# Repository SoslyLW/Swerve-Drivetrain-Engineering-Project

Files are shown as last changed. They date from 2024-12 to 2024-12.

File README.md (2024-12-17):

# Swerve Drivetrain Engineering Project
This repo contains the SOLIDWORKS model and reports for a swerve drivetrain developed for the Queen's University VEX Robotics Team, QVEX.

## Important Files
- The complete assembly of the drivetrain can be found at [`Solidworks Files > Drivetrain > Model.SLDASM`](https://github.com/SoslyLW/Swerve-Drivetrain-Engineering-Project/blob/main/Solidworks%20Files/Drivetrain/Model.SLDASM) 
- To see motion simulations of the wheel and gears in motion, see the file [`Solidworks Files > Motion Study > Motion With Materials.SLDASM`](https://github.com/SoslyLW/Swerve-Drivetrain-Engineering-Project/blob/main/Solidworks%20Files/Motion%20Study/Motion%20With%20Materials.SLDASM)
- The final project report can be see at [`Reports > SwerveDrivetrainFinalReport.pdf`](https://github.com/SoslyLW/Swerve-Drivetrain-Engineering-Project/blob/main/Reports/SwerveDrivetrainFinalReport.pdf)  (warning, it's 37 pages...)

## Explanation of a "Swerve Drivetrain"
**What is it?**

A swerve drivetrain is a type of drivetrain that can rotate it's wheels in any direction to allow complete freedom of motion.

**What types are there?**

There are 3 basic types of swerve drivetrains: direct drive, transmission, and differential. This design is a differential swerve drive.

**How does it work?**

In a differential swerve drive, each wheel is driven by 2 motors connected to 2 main gears (top and bottom) gear which are connected to 2 pinion gears which connects to the axle. When the 2 main gears rotate in the same direction, the wheel will turn in that direction. When the 2 main gears rotate in opposite directions, the wheel will spin according to the gear speed difference. By combining how you power the main gears you can make the wheel drive and turn in any direction.

See these examples below:

**Driving**

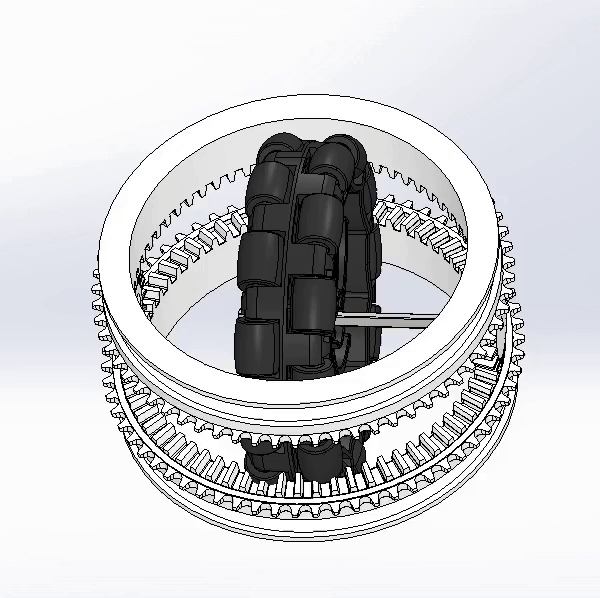
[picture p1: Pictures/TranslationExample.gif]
Wheel moving forward


**Turning**

Wheel turning

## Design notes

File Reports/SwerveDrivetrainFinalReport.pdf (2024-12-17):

# Swerve Drivetrain

# QVEX

# Group 737 Team A

## Arandjel Dimitrijevic

## Joellie Duffy

## Megan Marshall

## Avery McFadden

## Logan White

## Evelyn Morin

## Zach Elman

# April 4, 2022

### “We do hereby verify that this written report is our own individual work and contains our own original ideas, concepts, and designs. No portion of this report has been copied in whole or in part from another source, with the possible exception of properly referenced material”

i

## Executive Summary

When competing in VEX robotics, an effective and efficient drivetrain design is crucial to a team’s success. The QVEX team is interested in the use of a swerve drivetrain as this design produces a higher torque resulting in better competition results as opposed to other drives. A swerve drivetrain allows each wheel to have free rotation while being able to move forward. There are many configurations of the swerve drivetrain such as the direct, transmission, and differential drives. Through a decision matrix, the differential design was chosen over the direct and transmission due to their wiring and spacing challenges. Although this design is complex, its low profile and cost will give the QVEX team an advantage.

The differential drive has many 3D printed parts and can be easily implemented with the existing robot. The design features two aluminum mounting plates that encased the motors, wheels, and function as the mounting points to the chassis. There are also two gears (upper and lower) powered by a pinion gear attached to the motor shaft that provided torque through rotation and turned the robot by rotating at different speeds.

Custom base gears were designed to cater to the four-inch omni-directional wheel and the VEX generic chain and sprocket kit. The specific relations and measurements of these gears were calculated using research about VEX parts as well as bevel gears. The motor mounts and plates were also custom designed to account for specific height requirements, hole placement, and compatibility with the gear system.

The construction of the physical prototype was completed with some alterations due to unforeseen compatibility issues. The QVEX team was consulted to supply certain VEX parts, but the omni-directional wheels had rollers that exceeded four inches in diameter, and they were only able to supply high-strength chains. As a result, the design was altered to use a gear in the place of chains and a standard 4” wheel instead of an omni-directional one. The mounting plate and virtual model were updated to agree with the new design.

Testing was completed on the virtual model through various Solid works simulation software that analyzed the model’s motion, static capability, and sustainability. These sections and the financial analysis were all tested and scored appropriately based on quantifiable specifications that the group set earlier. All sections were scored from one to five, with a score given by how well the model performed in each of these sections. As a result, a scaled equation was used to combine the four sections into one number that determined whether the model was a successful swerve drivetrain. The model received a cumulative score of 3.4, meaning that client expectations were met and, in some cases, exceeded. For further implementation, it is recommended that the gear system is scaled for the omni-directional wheel and all metal parts are welded during construction.

ii

## Table of Contents

iii

iv

## List of Tables

Table 1: Table of stakeholders and their influence towards the project | 2
Table 2: Bill of materials for a quarter section of the swerve drivetrain | 5
Table 3: Decision matrix used to evaluate different swerve drivetrain configurations | 9
Table 4: List of purchased items and their costs | 14
Table 5: Work breakdown structure | 22
Table 6: Evaluation Rubric for the Testing Phase for the Model | 30

## List of Figures

Figure 1: Quarter section side view of the final differential swerve design | 4
Figure 2: Top view of a quarter section of the differential drive train | 4
Figure 3: CAD model of the final swerve drivetrain assembly, to be used in virtual testing | 5
Figure 4: Preliminary sketch of the direct drive | 6
Figure 5: Preliminary sketch of the transmission drive | 7
Figure 6: Original concept design for the differential swerve drive | 8
Figure 7: Physical prototype of the teams swerve drivetrain | 11
Figure 8: Static analysis of the bottom base gear | 15
Figure 9: Static analysis of the top the base gear | 15
Figure 10: Static analysis of the pinion gear | 16
Figure 11: Sustainability of the model using Japan as the region of exported materials | 17
Figure 12: Individual Contributions to the Phase 4 Report | 19
Figure 13: Timeline for the Client Presentation and Phase Three Completion | 23
Figure 14: Completion of the Status Reports and the start of Phase Four | 23
Figure 15: Timeline of the completion of Phase Four Part Two and the Design of the Drive | 24
Figure 16: Timeline for the completion of Phase Four and the design | 25
Figure 17: Timeline of the submission of Phase Four | 26
Figure 18: Original project timeline for the second half of the semester | 26
Figure 19: Timeline for the testing phase of the design | 27
Figure 20: Timeline for the testing phase of the virtual CAD and the build of the physical prototype......27
Figure 21: Reference diagram for gear calculations | 28
Figure 22: Measurements for hole placements on the motor mount and mounting plate. All
measurements in millimeters | 29

## Part 1: Key Information for Clients

## 1.1 Problem Statement and Scope Definition

### Problem Definition

VEX Robotics is a competition in which two teams of robots will attempt to score as many points as possible during the match to beat the opposing robots. During the latest competition, VEX points can be scored by placing rings on towers and moving the towers to a team's respective base. For many years VEX competitors have had two main drive trains, the tank drive and X drive configuration. The tank drive has more pushing power by keeping the wheels parallel to the direction of movement, whereas the X drive has less torque, but it can move and strafe in any direction. Alternately, the swerve drivetrain design can move in any direction with the wheels parallel to the movement allowing it to maximize the pushing force of the robot. The QVEX team is requesting a swerve drivetrain design as it will elevate their performance in competition in multiple ways.

### Problem Scope

With the given time and expectations from both the client and project manager, the group completed a CAD model of the swerve drivetrain that was tested through various simulations. The team physically constructed a quarter of the model to ensure that the physical prototype results resembled the ones obtained from the virtual testing simulation.

Client’s Needs
The client requested a swerve drivetrain, 18” x 18” in size, as noted in the VEX robotics competition guidelines. QVEX also requested that the drivetrain could maintain constant orientation while having complete operation mobility at no loss of speed or power. Since space was limited, the model required optimization in size, limiting moving parts and sturdiness. The client also suggested looking into gear ratios and power transfer methods to succeed in designing a successful drivetrain. As a final deliverable, a CAD (Computer-Aided Design) model of a single section of the drive was created and evaluated. Upon completion of the CAD model, a real version of the swerve was created. The model had to be tested as well, either using MATLAB or by physically building the model and completing testing in person. The swerve drivetrain was specifically chosen to maximize power and mobility, resulting in a more agile and competitive robot.

Constraints
- The drivetrain must be able to be built for under $100 and as light as possible (mostly 3D printed parts except for chassis and shafts)
- The drivetrain must be able to produce enough power to compete against other robots.
- All parts must be able to attach to the chassis without interfering with existing components
- The chassis cannot exceed 24” x 24”
- No more than 12 motors can be used while eight is the recommended amount

Functional Requirements
- Be able to switch between modes/directions of movement quickly and efficiently.
- Be able to have the wheels parallel to the direction of travel to maximize power like a Tank drive
- Be able to strafe and move in any direction like an X drive
- Be legal in competition
- The prototype is of at least one section of the drive
- Minimum 4 motors, maximum 12 (ideally 8)
- Build is recommended under 18” x 18”

Relevant Stakeholders
Table 1: Table of stakeholders and their influence towards the project
Stakeholder | Influence on the design process
QVEX | The team will use the design in competition, and it can improve their gameplay. Success in the competition will encourage more students to join the club and will increase funding from the university. The team has set out design requirements for elements they are looking to include such as wheels that are able to rotate independently and the robot is able to move in diagonal lines. The requirements laid out will ensure the drivetrain is compatible with the rest of their design.
VEX Robotics | The rules set out by the VEX robotics competition will constrain the design in terms of chassis/drivetrain size and available components.
Opponents | The opponents are looking to defeat the QVEX team by designing a robot with more torque, higher speeds, and greater ease of maneuverability. The clients' design must be stronger than the opponents in all aspects to defeat them. Since some opponents are expected to use tank-style drivetrains with more torque, this design must be optimized to have the ability to deliver as much torque as possible to maintain proper positioning while the opponent is attacking. The stake of the opponents overlaps with the stake that the Faculty of Engineering and Applied science holds. For the design to be superior to all opponents, it may become very costly and require materials the university isn’t providing.
Queen’s University Faculty of Engineering and Applied Science | The faculty will be investing in the QVEX design and gameplay. The design will need to be within the designated budget set out by the University. If the team is successful in their quest to build a robot containing a swerve drivetrain, it will provide the university with publicity, and presents the potential for the school to draw in more students eager to work and compete with QVEX. The stake of the faculty will overturn the stake of the opponents, without the funding provided by the university, the QVEX team would not be able to develop the design and compete.

## 1.2 Background Information

### Drivetrains

Designing any type of drive train poses the challenge of getting the power from the motor to the wheel. One way of transferring this power is using an indirect transmission system by attaching a belt to the shaft of the DC motor, then attaching that belt to the shaft of a caster. This can also be achieved using bevel gears which results in the motor undergoing far less stress [1]. In the chosen design, it means that the belt can be attached to the motor and then connected to the large driving gears that will be surrounding the wheels. While modifying the gears, the goal of having the swerve drivetrain with all four wheels turning, steering, and driven independently is still the number one priority. This allows the robot to move in any direction with its full pushing force, as the wheels can be parallel to the direction of movement. For a traditional swerve drivetrain to operate, there needs to be one motor to spin the wheel forward and one to pivot the wheel and change direction [2].

### Swerve Drivetrain

An issue commonly associated with swerve drivetrains is the lack of power output when the robot is turning [3]. This disadvantage can be minimized with the use of a differential swerve drive configuration. A differential swerve drivetrain has many advantages, such as it can use both gears to drive, which will allow the robot to have more power. This design takes advantage of the power output of the differential systems which will allow the team to spin the top gear and bottom gear at different speeds, effectively turning and powering the robot simultaneously. Another advantage of this design and using 3D printing is that it allows the drivetrain to be very compact as the larger gears can be placed very close together [4]. One drawback of the swerve drivetrain is that the mass is significantly higher than other drivetrain configurations [5]. The weight can be minimized by 3D printing as many parts as possible.

### Modeling

For modeling, the program SolidWorks is the most accessible and simple platform to use. The generic VEX parts (gears, belts, motors) can be downloaded and imported from any VEX CAD library which reduces design time since these parts can be complicated [6]. To simplify the online model creation, SolidWorks offers its own robotics section within the software that allows for simple and effective VEX construction [7]. SolidWorks also offers e-drawings that can be used to clearly show the client how the design operates from multiple angles, and if a physical prototype is not able to be constructed, these drawings can be used for the QVEX team to easily build it themselves.

## 1.3 Design Solution

The chosen design was the differential swerve drive. This was chosen based on criteria identified in the decision matrix, as seen in Table 3. More specifically, after many conceptual iterations, the team settled on the design see in Figure 1 and Figure 2.

In this design, the drivetrain is supported vertically using ball bearings placed on axles. Custom horizontal gears were designed with a groove on the outside for the bearings sit in to allow free, mostly frictionless movement. The two base gears are powered by motors that are mounted to the top mounting plate using custom motor mounts. The motors turn chains that interlock with teeth on the outside of the base gears.

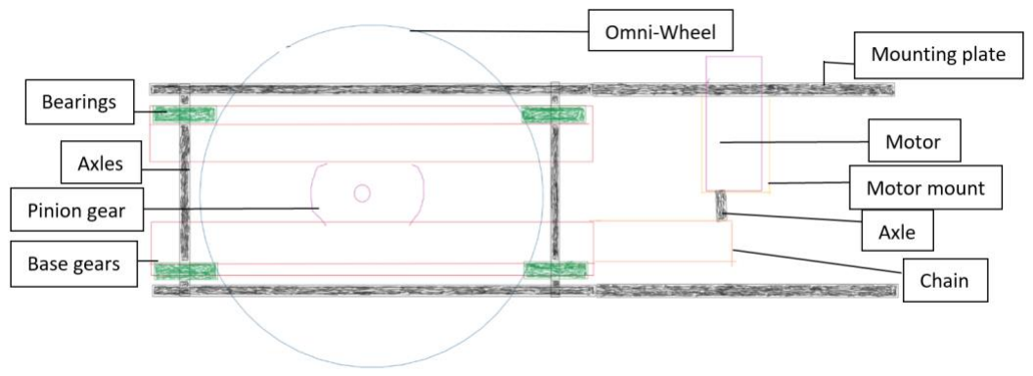
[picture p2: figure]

Figure 1: Quarter section side view of the final differential swerve design.

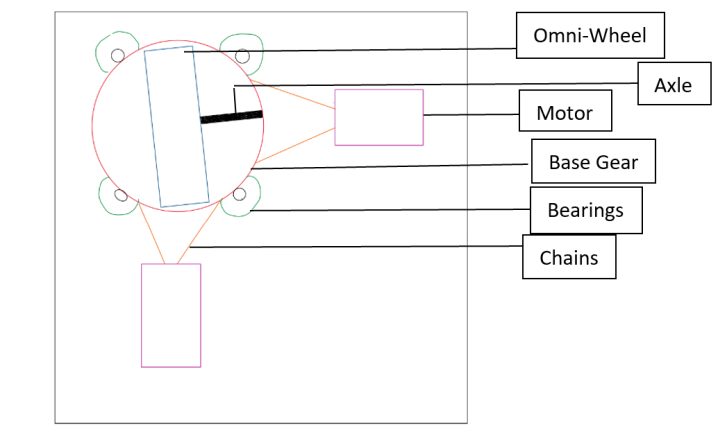
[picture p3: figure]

Figure 2: Top view of a quarter section of the differential drive train.

A CAD model was also constructed, which can be seen in Figure 3. The model was used in virtual testing to determine wheel speeds and the drivetrain’s ability to resist and support loads. The client will receive a copy of the CAD model, as well as a physical prototype. The physical prototype will display the ease of manufacturing, compactness, and whether the conceptual design will be successful once implemented. The CAD model will be used to demonstrate the drivetrains speed and turning capabilities.

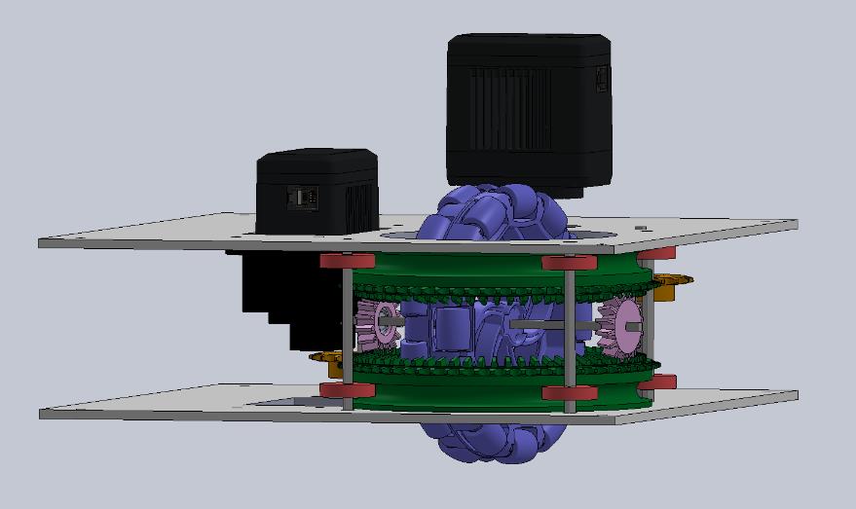
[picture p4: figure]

Figure 3: CAD model of the final swerve drivetrain assembly, to be used in virtual testing.

To implement the solution, the client would need to construct three more quarter sections, as well as mounting plates that cover the 18” x 18” base of the robot, instead of 9” x 9” sheets. Table 2 shows the bill of materials that was required to build a quarter section of the drivetrain. A written code would be required to control the speed of the individual motors, as well as the ability to reverse the direction of the motors to turn the wheels in both directions. To build the other sections, it would cost the QVEX team four times the costs outlined in Table 4, approximately $422, assuming they have access to VEX parts such as chains, motors, and wheels.

Table 2: Bill of materials for a quarter section of the swerve drivetrain.

Materials | Quantity
9” x 9” Aluminum Sheet | 2
22mm Round Radial Bearing | 8
4” Omni-directional Wheel | 1
3D Printed Custom Gears | 2
Bevel Gear | 1
Wheel Axle | 1
Bearing Axle | 4
VEX Motor | 2
VEX Chain | 2

## 1.4 Conclusions

The swerve drivetrain has intricate functions that can be executed with numerous different designs. Three main designs were considered in this project: the direct swerve drive, the transmission drive, and the differential drive. The final design was chosen based on important criteria such as cost, size, weight, and difficulty. Using a weighted decision matrix, the differential swerve drive design was found to be the best design for this project. A differential swerve drive is beneficial due to its low height and low cost. The final design is characterized by two outer gears that encircle the wheel with one upright gear between them that is attached to the axle and powers the wheel. These gears are custom designs that were 3D printed along with the motor mounts. Gears are used to power the upper and lower gears to turn and provide torque to the wheel. The wheel system is mounted to an aluminum sheet which can then be easily mounted to the chassis of the robot. Due to errors, the team went slightly over budget, spending $105.73.

The final model differed from the original design with a standard VEX wheel in place of the omnidirectional one as well as the chains being replaced with gears. These alterations were made due to incompatibility with available parts. To continue this design, it is recommended that the gear system is scaled to fit with the four-inch omnidirectional wheel. The bearings and shafts in the physical model interfere with the chain sprockets so it is recommended that thinner shafts are used with appropriate bearings of smaller inner diameter. The teeth on the upper and lower gears can be updated to be compatible with the high strength VEX chain to fulfill the original design if desired. Finally, it is recommended that the metal connections on the mounting plate are welded to ensure the longevity of the drivetrain.

## Part 2: Technical Information

## 2.1 Conceptual Design Solutions

### Design 1: The Direct Drive

This first drivetrain considered by the team was the direct drive swerve drivetrain. This design is characterized by a swivelling wheel where one motor is placed in line with the driving axle, attached to the swivel, and one motor is mounted directly to the chassis, as shown in Figure 4. The strength of this design is its simplicity. By mounting the driving motor in line with the wheel, there is no need for a transmission, drastically reducing the number of moving parts and thus the complexity. The design does have its drawbacks; one is that the wires connecting the driving motor to the chassis and VEX brain controller are unable to spin freely without tangling. To counteract this, the team went through an idea generating process and determined that a central hole through the swivelling axis would be necessary. Other design weaknesses include imbalanced loads on the axle and increased load on the turning motor.

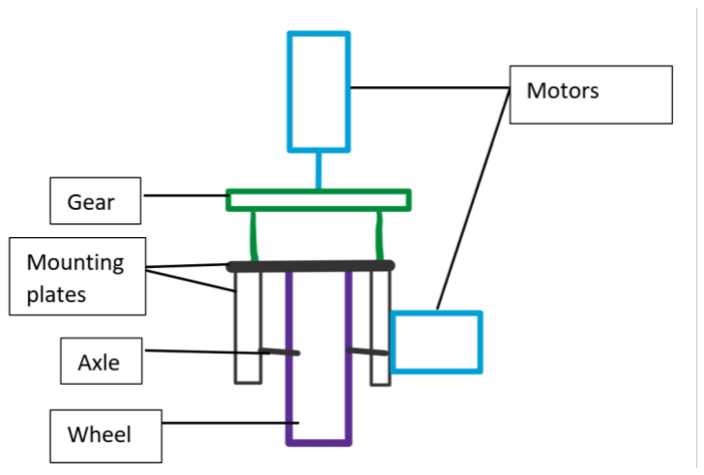
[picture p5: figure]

Figure 4: Preliminary sketch of the direct drive.

### Design 2: The Transmission Drive

The second drivetrain design conceived by the team is a type of transmission swerve drivetrain. This is another swivel-based design but features both the driving and turning motors mounted to the chassis as seen in Figure 5. Consequently, a gear-based transmission must be used to transfer the power of the driving motor to the appropriate axis. This aspect is one of the weaknesses of this design as it involves many moving parts with a need for high precision at every step. Having a transmission within a swivelling structure would also make the design much harder to repair should the transmission break. The advantage of this design is that it solves most of the issues associated with the direct drive design. This includes the issue of tangling wires, loads on the axle, and a decreased load on the turning motor.

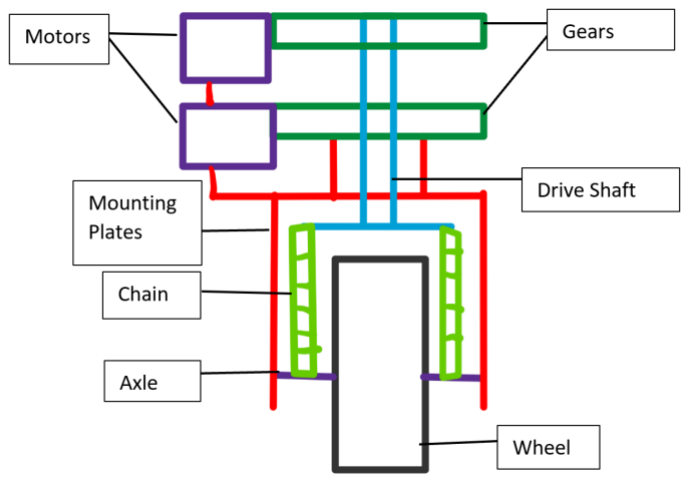
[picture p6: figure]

Figure 5: Preliminary sketch of the transmission drive.

It should also be noted that the first two design options require a large amount of vertical space. The client was consulted about this property of the designs and the team was informed that both designs are viable if properly implemented. However, if possible, the drivetrain should take up more horizontal space than vertical as to not interfere with components mounted to the chassis of the robot. This advice was considered in further idea generation and in the design evaluation matrix in Table 3.

### Design 3: The Differential Swerve

The third design option that was considered is the differential swerve drivetrain. This is a more complicated design that uses two larger horizontal gears placed around the wheel with a vertical bevel pinion gear attached to the wheel axle, in between the two horizontal gears. Each larger gear is driven independently with its own motor, allowing for differing velocities among the large gears. If the gears are moving at the same speed and in the same direction, the wheel will rotate. If the larger gears have differently velocities, the wheel will spin according to the relative difference in speed. A diagram is shown below in Figure 6. The advantages of this design are that the gears can be placed overlapping the wheel and that the motors can be placed alongside the wheel with relative ease, drastically reducing the vertical footprint of the design. Additionally, by not allocating one motor for turning and one for driving, the max turning and driving speed is increased. The drawbacks of the design are its need for custom designed gears to integrate with the rest of the robot, a time-expensive process, and the lack of space to mount and install all the components without sacrificing the benefits of the design’s compactness.

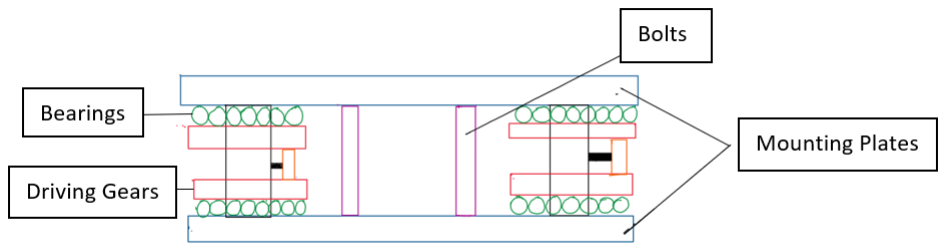
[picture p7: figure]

Figure 6: Original concept design for the differential swerve drive.

## 2.2 Decision Making

A decision matrix, as seen in Table 3, was used to compare the three design options. Each design was analyzed based on the cost, weight, complexity, and compactness. Every aspect was rated on a scale of 1-4, with the highest overall score being 16. Through this process, the team chose the differential swerve as the design proposed to be implemented due to its low weight, minimal vertical height, and low cost.

Table 3: Decision matrix used to evaluate different swerve drivetrain configurations

| Differential Swerve | Direct Drive Swerve | Transmission Swerve
Weight Optimal weight of 10lbs, maximum weight of 30 lbs [12]. | Weighs approximately 12 pounds for four-wheel design [13]. 3 | Weighs approximately 20 pounds for four-wheel design [14]. 2 | Weighs approximately 21 pounds for four-wheel design [15]. 2
Compactness Design occupies the least amount of vertical and horizontal space. | All parts will be within the height of the 4” wheels. Will be approximately 5” long by 5” wide. 4 | Design is approximately 5.5” wide, and 9.5” tall with the motors included [16]. 3 | Approximately 10” tall by 5” wide, as they allow space for the wheels, motor, and gears in the vertical direction. 2
Ease of manufacturing/ Implementation Minimize number of custom parts required, and ease of drivetrain assembly | Will be made of mostly custom 3D printed parts; however, it only consists of about 15 pieces per wheel and will be simple to assemble. 3 | Majority of parts will be made of existing metal to ensure structural integrity, can be quite complex to assemble and once assembled still has issues such as loose/excess wires. 2 | Requires many custom metal parts. The complex design will also make it very challenging to assemble. 2
Cost to Manufacture Maximum budget of $100. | Cost of 3D printed parts will be $30, and the additional metal pieces will be around $30 [8] [9], with an overall cost of $60. 4 | Majority of metal pieces need to be purchased, resulting in costs up to $120 [10]. 1 | The custom fabrication of many metal parts will exceed $180 [11]. This will exceed the set-out budget. 1
Final Weighting | 14 | 8 | 7

The low weight, minimal vertical height, and low cost make the differential swerve drivetrain the optimal solution. The differential is the design capable of producing the highest speeds and outputting the most torque, while also being relatively simple to manufacture and assemble. Due to its compactness, it is the ideal solution for QVEX which will allow them the most freedom when constructing the other components of their robot. There are also many varying components of the differential drivetrain that can be customized to fit to the exact specifications the team may be looking for. Within the differential, the team had to conclude which mounting and power transmission options would be implemented. These options have been weighed below.

### Mounting Options

Within the differential design, the team investigated different mounting options for attaching the drivetrain to the frame and the rest of the chassis. The first option investigated by the team was to use ball bearings to vertically support the gears. This would see each gear sitting on top of a mounting plate with channels in both the gear and mounting plate for the ball bearings. Unfortunately, the team could not find any VEX-approved ball bearings, so this solution was deemed inviable. The second and chosen option was to support the gears by using shafts fitted with horizontal bearings. These bearings fit into a channel in the side of the gears, allowing them to spin while being supported vertically. Since VEX does sell their own style of radial bearings, this design would both meet the team’s need and be legal as per the project constraints.

### Power Transmission Options

There were several different methods of power transmission considered for transferring the motor power to the gears. The first option was to use a gear coming directly from the motor and attach to teeth on the side of the large gears. While this option is straightforward, it lacks flexibility presented by the other options. It would necessitate a definitive placement of the motors and the gear ratio between the motor gear and the swerve drive gear would need to be fixed. The second option considered was to use a belt system attached to the motor, and around the large gears. This was eliminated due to the fear of the belt slipping and that it would also necessitate definitive motor place. The third and final power transmission method examined was a chain-based method. This was decided to be the best as it performs very similar to a belt drive with a few key advantages. Chain drives do not struggle with the same slippage as belt drives, can be shortened or lengthened to support different motor placements in the case of unexpected problems, and can be altered for behavioral adjustments.

## 2.3 Implementation

### Preliminary design

The work done after Phase 3 followed the original timeline other than the changes stated in the Contingency Plan. Due to the delay of obtaining the required physical parts, the group had to alter aspects of the design to meet the project deadline. The main dependency of this design is the custom bevel gears; hence, these were designed first. The custom gears were carefully designed with the help of supporting research that ensured the bevel-style gears would interlock properly. These calculations can be found in Appendix IV: Calculations with the corresponding diagram indicating the locations of measurements. To confirm the gears fit together, a preliminary model was constructed of the gear subsystem in SolidWorks. The system had few errors when assembled originally with only the teeth needing to be edited to account for rotational interference.

Following the design of the gears, the motor mounts and mounting plates were created, as the gears defined the specifications of these parts, such as heights and hole placements. Preliminary
measurements for the mounting plates that corresponded with the use of chains are shown in Figure 22, found in Appendix IV: Calculations. An assembly was made that included all parts of the system with imported files from the VEX website for the motor, shafts, and wheel.

### Considerations

When planning the building process for the physical model, the environmental impact of the design was taken into consideration. Since the project is a one-time-use model, it was important that many of the parts were recycled or could be used again in the future. The standard VEX parts were re-used from previous robots and other parts, such as the bearings, were minimally altered to allow for re-use in future projects. The design and testing process were created to be sufficiently thorough so that the QVEX team could implement a swerve drive into their future robots. With the ability to create a swerve drivetrain, the team could have a higher level of achievement in competition and in turn receive more funding from the university as well as inspire new team members to join. During the building process, safety precautions were taken to ensure all members were protected from harm. Safety glasses were always worn within the workshop, earplugs were worn while drilling and cutting the metal sheets, and nonworking members stayed a safe distance away from working members.

### Construction and Alterations

Since some parts of the system were unable to be printed or manufactured, the QVEX team was consulted to supply these parts. Due to 3D printing deadlines, this unfortunately happened after the custom parts were created. As a result, there were issues with the custom gears being compatible with supplied parts. When designing the base gears, a four-inch standard VEX wheel was used, however, the QVEX team was only able to supply a four-inch omni directional wheel. This wheel was incompatible with the design as the rollers on the wheel cause the diameter to be larger than four inches. For the physical model, a four-inch gear was used to simulate the function of the correct wheel so testing could proceed. The custom gears were also designed to be compatible with the basic VEX chain, however, the QVEX team could only provide the High-Strength chain, which was incompatible with the teeth created. To solve this issue, the design was altered to use gears instead of chains. These gears were 3D printed for efficiency and to ensure compatibility. The CAD assembly was altered as well by adding the correct gears and updating the mounting plate holes to account for this change. The overall model, which can be seen in Figure 7, was constructed with the implementation of these changes and was successfully completed.

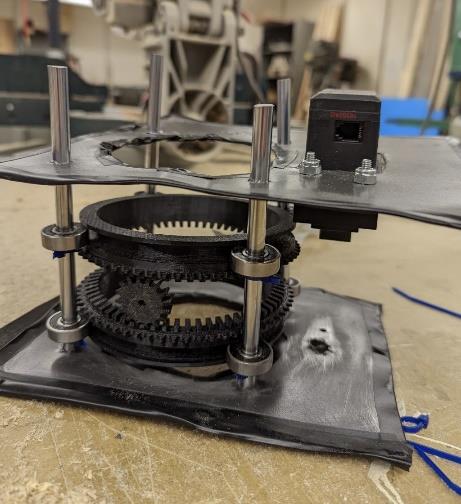
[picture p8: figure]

Figure 7: Physical prototype of the teams swerve drivetrain.

### Testing Process

After the construction of both the physical prototype and the virtual model, only the virtual model was tested to ensure the functionality of the design. The overall testing was separated into four sections for increased efficiency and organization. The first section was the motion study, which tested that the gear and wheel speeds matched the calculated predictions. The second section was the static simulation, which tested that the design could sustain the load of the robot and any unexpected exterior forces. The third section was about the sustainability and materials used, ensuring that the drive was not harmful to the environment during disposal and that the swerve could be easily reconstructed from anywhere in the world. The quantification of each section is shown in

Appendix V: Evaluation Rubric. The specific quantification of certain criteria was judged based on relative statistics given by a swerve drive with a design like the proposed model [1]. Due to unforeseen errors such as bending as a result of fabrication of the metal sheets, the physical model was unable to be tested. To provide a thorough analysis, the virtual model was more rigorously tested than originally planned with the alteration that resulting values were unable to be compared to the real system.

The virtual modelling was run on the same software that the CAD was designed in. The SolidWorks Dassault System simulation software offers a VEX tutorial course that was used by the team to efficiently test the swerve drive up to VEX standards [7]. The testing of this design focused on the functionality of the gear system, evaluating whether it can effectively spin and rotate the wheel. This specification allowed for the external parts of the system like the mounting plates, bearings, and their respective mounting shafts to be omitted. Since a simulation was used, the motor parts were replaced with simulated motion that is equivalent to what is produced from the VEX motors. After, each section (motion study, static analysis, sustainability, and financial requirements) was calculated using a weighted average using (1):

Final Score = AVGMS ∗ (0.5) + AVGSA ∗ (0.4) + AVGSUS ∗ (0.05) + AVGFR ∗ (0.05) | (1)

AVG means the average score of the motion study (MS), static analysis (SA), sustainability (SUS), and financial requirements (FR) respectively. The weightings are due to the client’s needs and that they are looking more for a functioning swerve drive that can sustain the load of their robot rather than a swerve that is very good for the environment. A final score of 1 will determine that the group has been unable to meet any needs given by the client. A score of 2 reveals that the group has made a valiant attempt but is still not quite at the level that the client requested. A score of 3 determines that the group has met all the client’s needs. A score of 4 determines that the group has exceeded the client’s expectations in most categories and that the client will be very satisfied and a score of 5 determines that the client would want to implement this design on the QVEX robot immediately. A final score of at least 3 will determine that the group has succeeded in meeting the client’s requirements and thus, has succeeded in the design.

## 2.4 Project Plan

### Work Breakdown Structure

Throughout the duration of this term, there were some events that occurred that caused a delay in project progression. This includes things like a delay arrival for the 3D printed parts, booking and software issues and many more uncontrollable variables. The team did mitigate these events at the start of the term and fell back on the second plan provided in

## Appendix III: Updated Gantt Chart and planned an updated work breakdown structure provided in

Appendix II: Project Plan.

### Risk Mitigation

After assessing the risks associated with the project completion, there were some that the group was able to mitigate. Unfortunately, due to uncontrollable errors and obstacles, there were some events that caused the group to halt or even reverse the project progression. One of these obstacles was the overall process of obtaining the physical parts to build the swerve. Due to unforeseen delays in delivering the high-strength chain, the group was forced to change the design late into the project as it was more important to have a working prototype rather than relying the entire design on one part being delivered late. As a result, the group was forced to re-iterate a design that did not implement the high-strength chain. Some risks that were mitigated with caution by the team on a consistent basis was the work done on the virtual CAD. SolidWorks is a computationally intensive program that often causes a lot of crashes at random times. The group made a valiant effort to save every file and send copies to one another so that if there was a surprise crash on the program, there would not be major setbacks in progression and backups would be available.

### Contingency Plan

The original contingency plan was that there would be two rounds of testing done on the virtual model if a physical prototype was not completed by the given deadline. Although there was an obstacle in the progression of the construction of the physical model, the group still proceeded with its construction and ran the virtual tests simultaneously to complete both by the given deadline. This was done so that the client can still have a physical prototype along with the virtual CAD model.

### Potential Changes

If this project was to be done again with the knowledge the group has now as well as assuming that the first two thirds of the project timeline was spent in person rather than online, there would be significant changes made to the design. Online communication was the root of most of the team’s obstacles since there was no simple way of getting ideas and designs across through a screen. Having team meetings take place in person from the beginning would have helped the team tremendously in having accurate specifications to the design and assuring that every group member understood what was expected of them. Although the team was content with the number of meetings that were held during the week, a change that would be made is having more meetings being centered around the production of the swerve rather than report writing. With that point being stated, having the meetings held online made it difficult to make major strides in the project completion when it is impossible to have any sort of design and implementations being made to the design when every group member is working remotely.

## 2.5 Financial Analysis

Many of the parts used in the build were recycled and therefore came at a discounted cost. The omnidirectional wheel, VEX chains, and axles were recycled from a previous robot. The VEX motors were acquired from the QVEX team with no cost. Unfortunately, due to a printing error, the original bearings and shafts purchased were incompatible, thus bearings and shafts of the correct size were purchased. This error accounts for the higher cost than previously expected. To save cost, the aluminum sheets were fashioned out of baking trays. All members of the team acquired safety trained in the shop to cut and drill the aluminum sheets at no cost.

Table 4: List of purchased items and their costs

Item | Price
Bearings | $24.27
Shafts | $29.48
Printing | $30.00
Baking trays | $21.98
| Total
| $105.73

Due to most of the project being recycled parts from previous robots, the build has a low cost in comparison to other solutions. When implementing this design, it will cost the client approximately four times what was outlined in Table 4, coming to a total of $422.92. The client may be able to save money when implementing this design if they have access to similar materials and resources, but at a discounted price.

## 2.6 Evaluation

Evaluation was done through SolidWorks simulation software. In terms of the motion study, using the gear ratio of 18:64 and a 4-inch omni-directional wheel, the model achieved a constant a velocity of 3.59m
s

. This performance scores a 3 when referring to the

Appendix V: Evaluation Rubric and meets client expectations. This result implies that the QVEX team can rely on the swerve drive’s ability to move and rotate effectively in competition at a pace that is up to their expectations.

In terms of the static analysis section, when applying a force of 270N (about 27.55kg) which is the average weight of a robot, the Solid Works static analysis simulation software produced the following stress diagrams, seen in Figure 8, Figure 9, and Figure 10. The base gears follow the teams’ expectations as the bottom gear should have most of the load placed where the pinion gear attaches, as depicted in Figure 8. The rest of the structure has an even distribution for load capabilities which concludes that the bottom gear will not undergo failure when the rest of the robot is built.

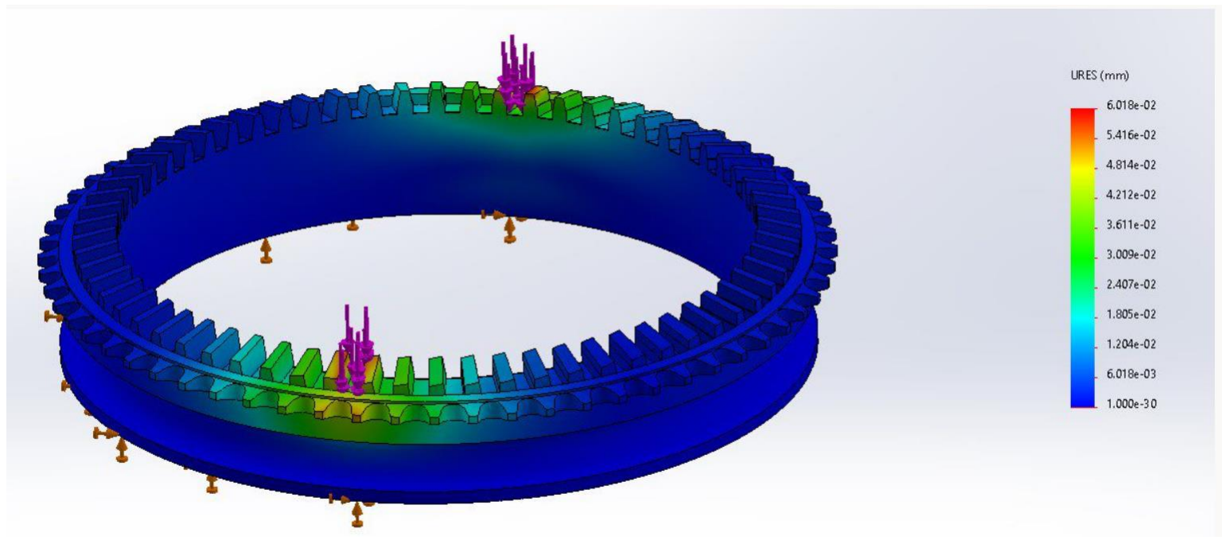
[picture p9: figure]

Figure 8: Static analysis of the bottom base gear.

The top base gear will experience a symmetrical load downwards from the weight of the attached QVEX robot and chassis. The SolidWorks analysis shows that the deflections cause by this load will be minimal using the properties of the material. The higher amount of deflection in parts of the gear are cause by the nature of how the gear is supported. Where the displacement in Figure 9 is lowest corresponds to where the two pinion gears attach to the top gear.

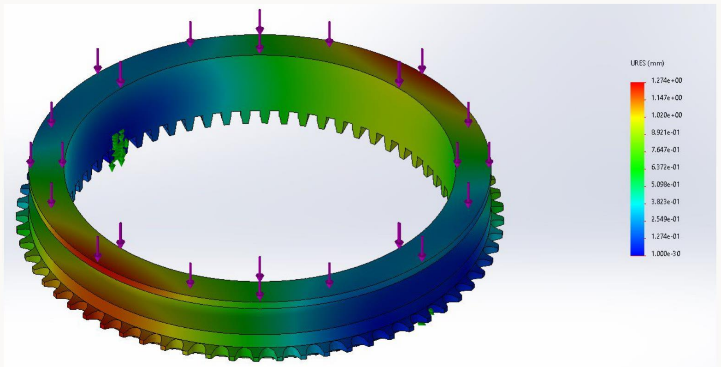
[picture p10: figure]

Figure 9: Static analysis of the top the base gear.

As for the pinion gear, for the applied load to the top gear, the pinion gear will experience a portion of the force where the pinion gear contacts the larger gear. Since there are two pinion gears in the design, the overall load is halved. Also of note, since the system is in equilibrium, the pinion gear will experience an equivalent 135 N force from the bottom gear, resisting the force that the pinion gear applies to it. The result of these forces can be seen in Figure 10. Having this symmetrical load distribution and having the pinion gear be centrally fixed through the shaft means that the pinion gear will also not slant and will be able to sustain the load of the top base gear.

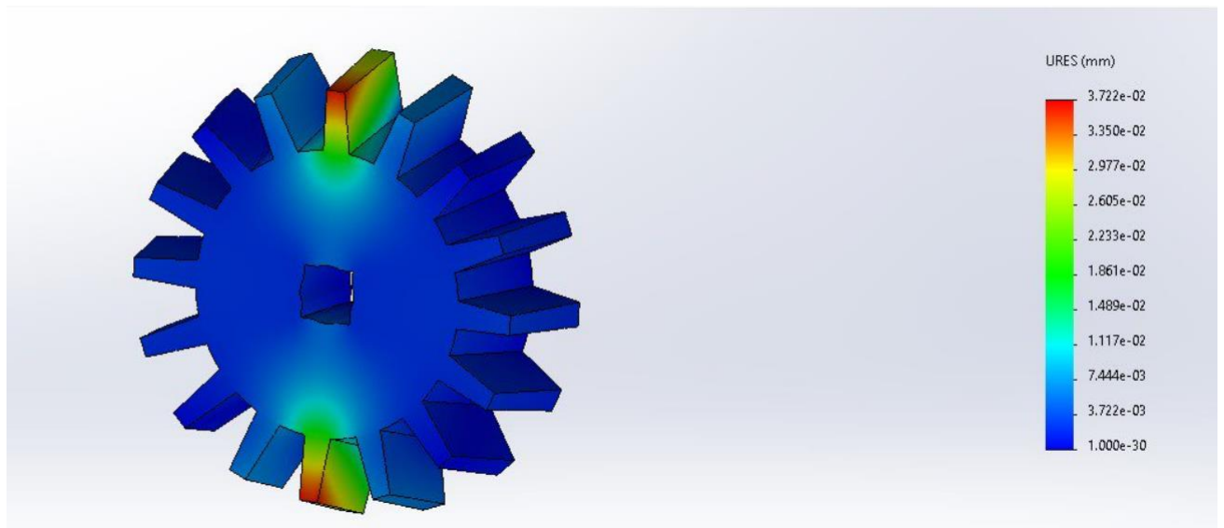
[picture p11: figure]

Figure 10: Static analysis of the pinion gear.

Having these promising results concluding from a load of 270N, the model easily scores a 5 in the evaluation scoring. As for the area expectations, the area was calculated by taking the dimensions of a single mounting plate and multiplying each side by two to factor in that there will be four of these models made for the overall robot. This brings the dimensions of the overall frame to 17.98” x 17.98”. Although this does meet the clients’ expectations and QVEX rules, it still has some room for optimization and will only score a 3 in that section. This brings the overall scoring for the static analysis section to a 4 because although the model can withstand heavy loads and still have structural integrity, the area of the model has not reached full optimization just yet.

The sustainability was tested using the SolidWorks life cycle software where multiple import sources were tested and various length times were used to find the optimal statistics to assure that the model does not cause severe environmental damage.

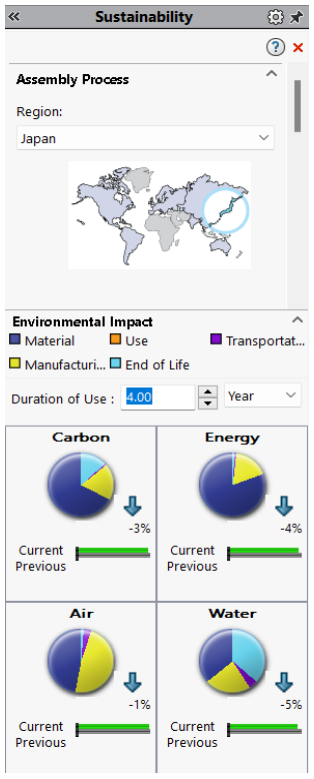
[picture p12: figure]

Figure 11: Sustainability of the model using Japan as the region of exported materials.

Multiple regions of material extraction were tested and considered. Japan showed the best results assuming that the team would be using this model for the next four years consistently. As a result, the carbon footprint of the model is 2.4kg after four years which scores a 3 in the evaluation scoring. For the financial section, although minimal printing sessions were required, the group did go over budget and thus resulted in a score of 2.5.

### Results

Using the scoring equation (1) provided in Testing Process, the final model had the following scores: Motion study scored a 3, static analysis scored a 5, sustainability scored a 3, and financial analysis scored a 2.5. Overall, using the weighted scaling, the model scored a 3.4. This concludes that the group has succeeded in meeting the clients’ expectations and that the client will be satisfied with the model as it will offer optimal motion and load bearing capabilities. The only downside to this design is that it will be expensive and the QVEX team will have to prioritize their budget toward the swerve design. Overall, the groups work over the semester paid off as a successful swerve drivetrain was designed and validated through testing.

## References

[1] StackExchange, "Calculating motor Torque and RPM Requirements for Swerve Drive," StackExchange, [Online]. Available: https://robotics.stackexchange.com/questions/22853/calculating-motor-torque-and-rpm-requirements-for-swerve-drive. [Accessed 20 Feb. 2022].
[2] D. Roman, "Academia," Omnidirectional-Drive-Systems, p. 36, 2006.
[3] Autodesk Inc., "Autodesk's VEX Robotics Curriculum: Advanced Gears," October 2012. [Online]. Available: https://www.fhrangers.org/cms/lib/PA01001569/Centricity/Domain/1116/VEX%20-%20Unit%207.pdf. [Accessed 29 Jan. 2022].
[4] S. Ryckman, "Swervebot," Rockerbotics, [Online]. Available: http://robotics.sdsmt.edu/projects/swervebot. [Accessed 5 Feb. 2022].
[5] "Swerve Central," Team 1640, 19 November 2019. [Online]. Available: http://team1640.com/wiki/index.php/Swerve_Central. [Accessed 28 Jan. 2022].
[6] VexPro, "DriveTrain Design Guide," 2014. [Online]. Available: https://content.vexrobotics.com/vexpro/pdf/Build-Blitz-2015-Drivetrain-Design-Guide-rev3.pdf. [Accessed 27 Jan. 2022].
[7] SolidWorks, "Robotics Tutorials," SolidWorks, [Online]. Available: https://www.solidworks.com/sw/education/9931_ENU_HTML.htm. [Accessed 20 Feb. 2022].
[8] Hilitand Store, "10Pcs MR115-2RS 5x11x4mm Miniature Ball Bearings, Steel Bearings, Used for 3D Printers, Model, Skateboard, Roller Slip," Amazon, [Online]. Available: https://www.amazon.ca/MR115-2RSMini-Bearings-Double-Shielded-Replacement-5x11x4mm/dp/B07CVBW44R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. [Accessed 24 Mar. 2022].

[9] Utoolmart, "Utoolmart Round Steel Rod, 5mm HSS Lathe Bar Stock Tool 100mm Long, for Shaft Gear Drill Lathes Boring Machine Turning Miniature Axle, Cylindrical Pin DIY Craft Tool, 10pcs," Amazon, [Online]. Available: https://www.amazon.ca/Utoolmart-mmSpecial-White-Turning-Carving/dp/B07Y81SB2T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. [Accessed 24 Mar. 2022].
[10] "VEX Robotics," [Online]. Available: https://www.vexrobotics.com/aluminum-kits.html. [Accessed 24 Mar. 2022].
[11] K. W. Mikesell, "Costing and Pricing it Right," The Fabricator, 8 April 2019. [Online]. Available: https://www.thefabricator.com/thefabricator/article/shopmanagement/costing-and-pricing-it-right. [Accessed 24 Mar. 2022].

## Appendix I: Contributions

Figure 12: Individual Contributions to the Phase 4 Report.

Task | Description | Person Assigned | Duration
Creating Final Assembly | Creating an assembly in SolidWorks to ensure proper fitting and intended design of all individual components. | Arandjel | 2 hours
Testing CAD model | Running virtual load and motor simulations in SolidWorks to ensure design will meet clients needs | Logan, Arandjel | 9 hours
Building Physical Prototype | Constructing a physical prototype of the design using 3D printed parts. Includes time spent manufacturing custom made mounting plates in the design shop. | Joellie, Megan, Avery | 6 hours
Executive Summary | Summary of the objective of the project, scope of the research/design, brief description of the decision process between the different designs, the final chosen solution, the results of any testing/evaluation thus far. Should be understood by a non-technical reader. | Megan, Arandjel | 1 hour
Table of Contents | Created the table of contents and updated consistently before submitting. | Joellie | 5 minutes
List of Figures and Tables | Made the list of figures and list of tables. Also updated it consistently before submitting. | Logan | 15 minutes

Problem Statement and Scope Definition | Updated version from Phase 3. Any changes made were stated and briefly explained. Also updated quantifiable specifications based on feedback received from Phase 3. | Avery | 1 hour
Background Information | Condensed the information summary from Phase 2 and Phase 3. Also provided a summary of any new information that was acquired that affects the design. Also assured to only keep the information that is relevant to the rest of the report. | Megan, Avery | 30 minutes
Design Solution | Provide a thorough but concise design solution that was undertaken. The design solution was described to the client effectively. The deliverables resulting from the project (CAD model, physical prototypes) were discussed. Any next steps to the client on how to implement the solution was outlined and the final financial information (expected costs) was summarized. | Joellie | 1 hour
Conclusions | Summarized the information so far in the report. Also described recommendations for continuing the design and how the group would change any outcomes given the opportunity. | Megan | 1 hour
Conceptual Design Solutions | Updated, edited, and condensed from Phase 3. Described the possible design solutions. The description included the multiple approaches that were taken (different mounting solutions, chain versus belt versus gear). | Logan | 1 hour
Decision Making | Updated and condensed from Phase 3. The original assumptions that were made were revisited and any changes were described. | Joellie | 45 minutes
Implementation | The work done after Phase 3 that was not mentioned in the Design Solution section was described. The procedure of how the problem was solved was presented and changes made from the original proposal in Phase 3 was described. Any societal and | Megan | 2 hours

| environmental factors that impacted the design process was mentioned as well as the modelling used to further the design.
Project Plan | Any changes made to the timeline were identified. Included a table of the updated work breakdown table with a column explaining significant differences planned and the actual hours spent on certain tasks. An updated Gantt chart was included. Described what would be done differently if the project was to be done again. Described what happened to the risks stated in Phase 3. | Arandjel | 1.5 hours
Financial Analysis | The cost and financial benefits to the solution were discussed. Discussed any costs that the group had up until now. A breakdown of materials used to build the prototype was stated. | Joellie | 45 minutes
Evaluation | The outcome of the project and the objectives a quantifiable specification stated in the problem statement were compared. Any final tests to validate the design was included as well as an evaluation rubric included in the appendix. | Arandjel | 2 hours
References | Created the references section. | Logan | 30 minutes
Appendix | Created the individual contributions table and formatted all the appendices in ascending order. | Arandjel | 25 minutes

## Appendix II: Project Plan

Table 5: Work breakdown structure

Task Identifier | Description | Duration-Expected (days) | Duration-Actual (days) | Leader
1 | Problem Definition | 7 | 7 | Avery
1.1 | Meet with client to outline problem | 1 | 1 | Project Manager
1.2 | Identify stakeholders | 1 | 1 | Megan
1.3 | Create team contract | 2 | 2 | Arandjel
1.4 | Identify required research | 3 | 3 | Avery
2 | Preliminary design | 18 | 18
2.1 | Background research | 4 | 4 | Logan
2.2 | Create three design options | 4 | 4 | Avery
2.3 | Choose final design | 3 | 3 | Joellie
2.4 | Preliminary sketches | 2 | 2 | Megan
2.5 | Prepare for client presentation | 5 | 5 | Arandjel
3 | CAD creation | 21 | 31
3.1 | Research and complete necessary calculations | 7 | 7 | Megan
3.2 | Create preliminary CAD files | 7 | 12 | Joellie
3.4 | Finalize CAD files | 3 | 2 | Logan
3.4 | Create CAD assembly | 5 | 10 | Arandjel
4 | Building | 3 | 2
4.1 | Machine required parts | 2 | 1 | Joellie
4.2 | Assemble material parts | 1 | 1 | Avery
5 | Testing | 14 | 7
5.1 | Simulation test with 3D model | 3 | 2 | Arandjel
5.2 | Test real model | 3 | 0 | Megan
5.3 | Evaluate simulation results | 3 | 3 | Logan
5.4 | Evaluate real model results | 3 | 0 | Avery
5.5 | Create solutions and next steps | 2 | 2 | Joellie

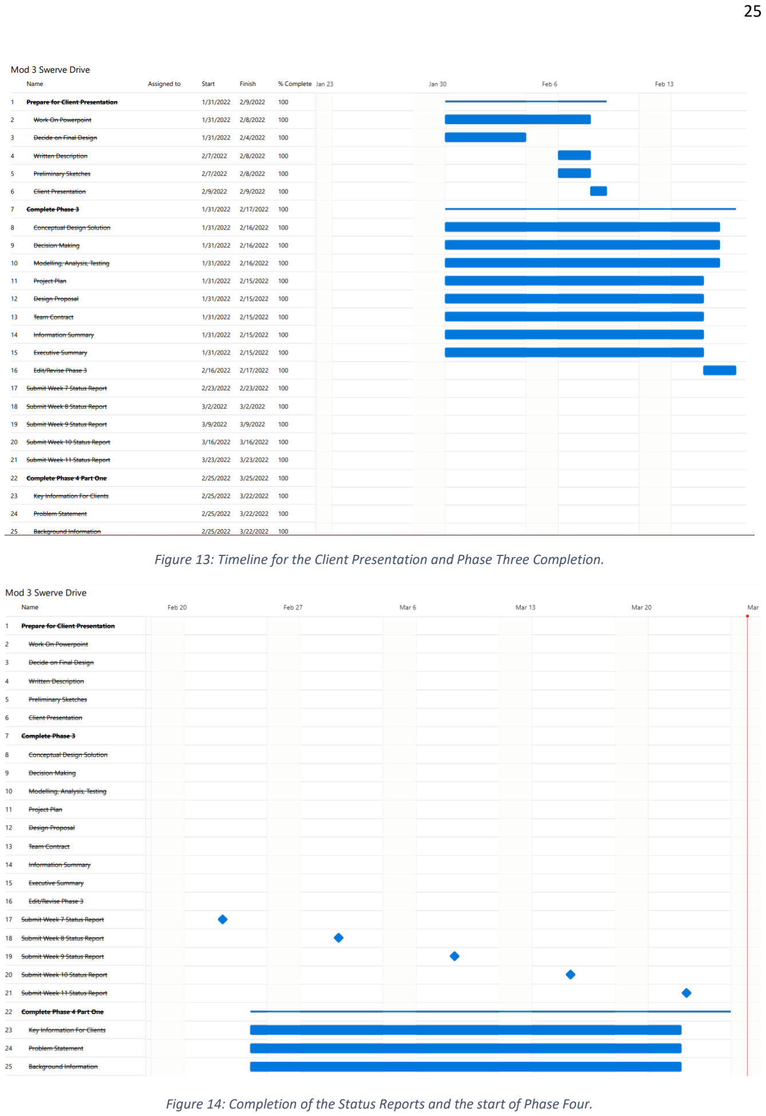
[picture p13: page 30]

Figure 13: Timeline for the Client Presentation and Phase Three Completion.

Figure 14: Completion of the Status Reports and the start of Phase Four.

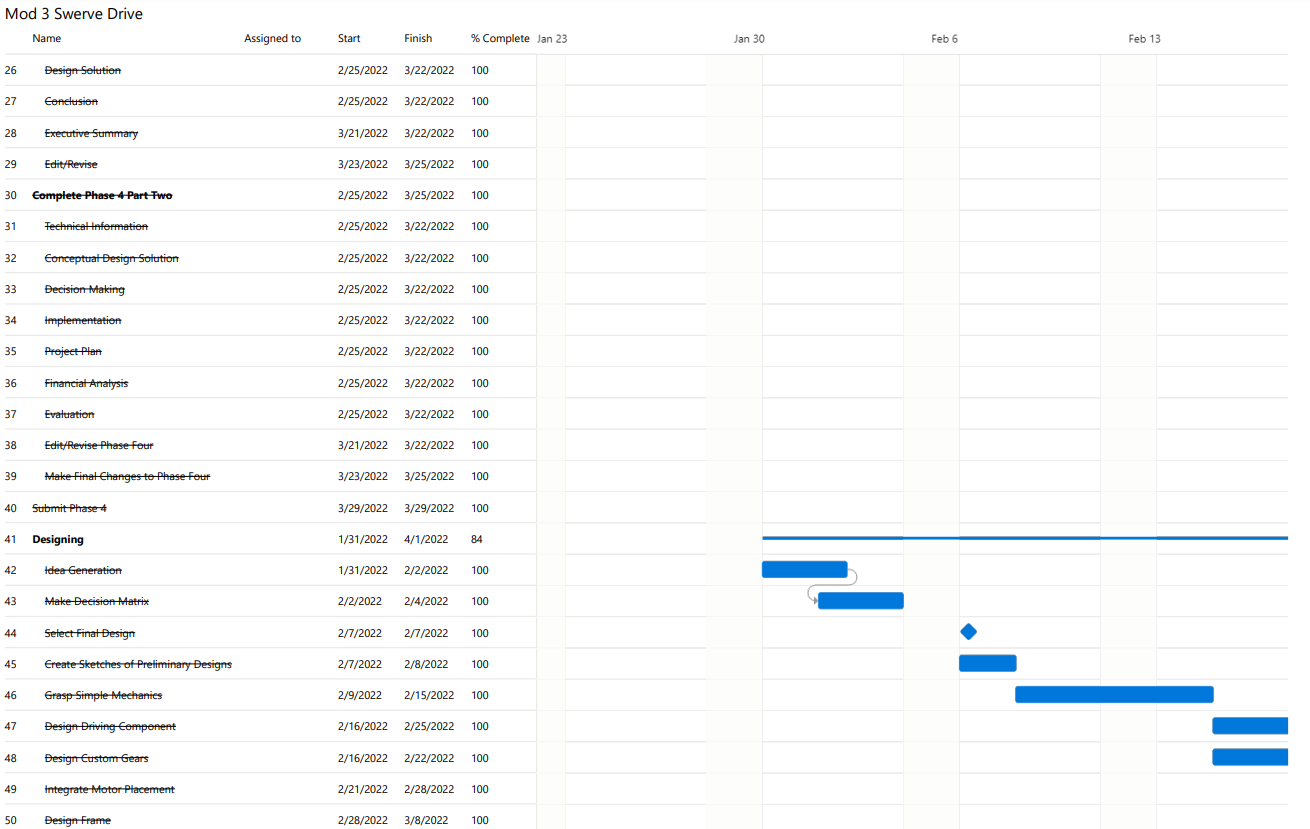
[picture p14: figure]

Figure 15: Timeline of the completion of Phase Four Part Two and the Design of the Drive.

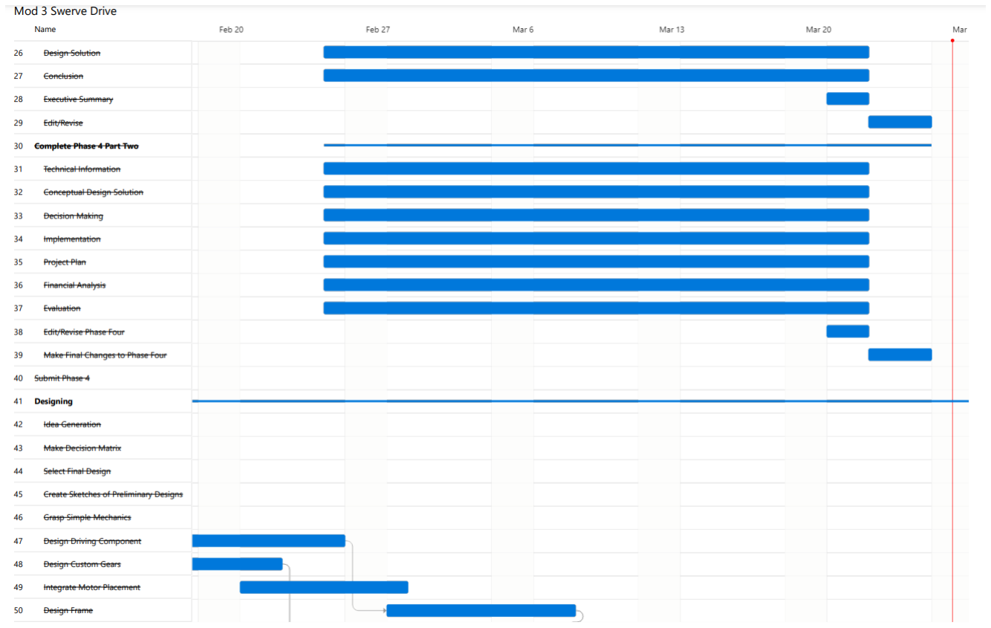
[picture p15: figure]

Figure 16: Timeline for the completion of Phase Four and the design.

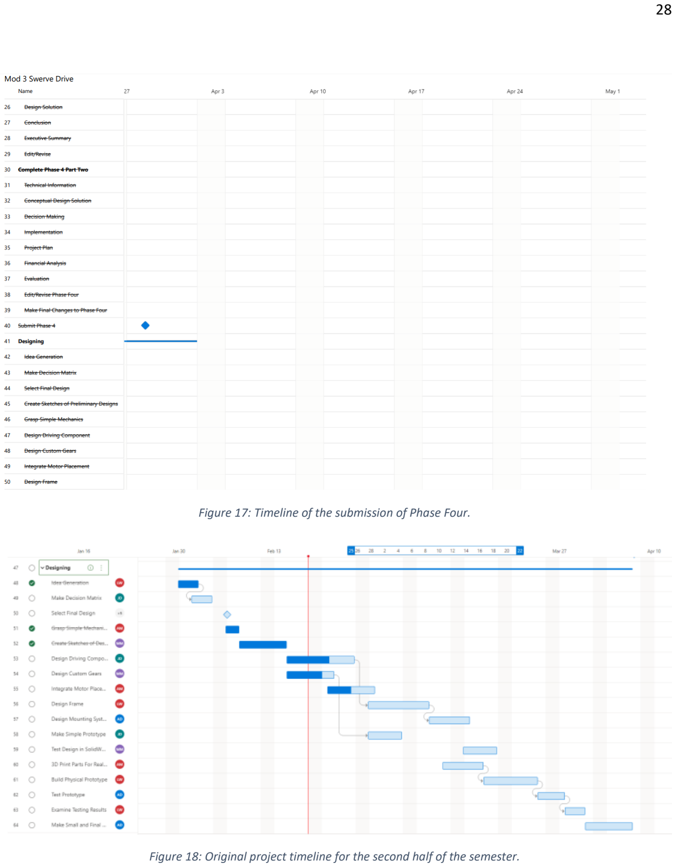
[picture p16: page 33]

Figure 17: Timeline of the submission of Phase Four.

Figure 18: Original project timeline for the second half of the semester.

## Appendix III: Updated Gantt Chart

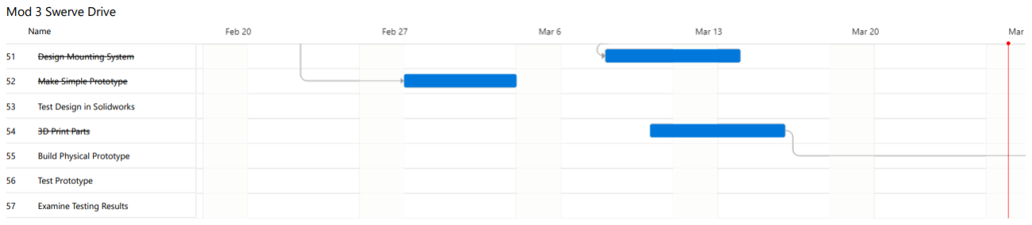
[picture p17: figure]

Figure 19: Timeline for the testing phase of the design.

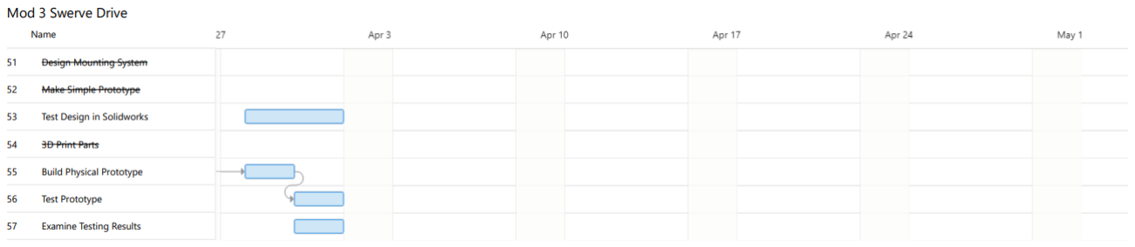
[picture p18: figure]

Figure 20: Timeline for the testing phase of the virtual CAD and the build of the physical prototype.

## Appendix IV: Calculations

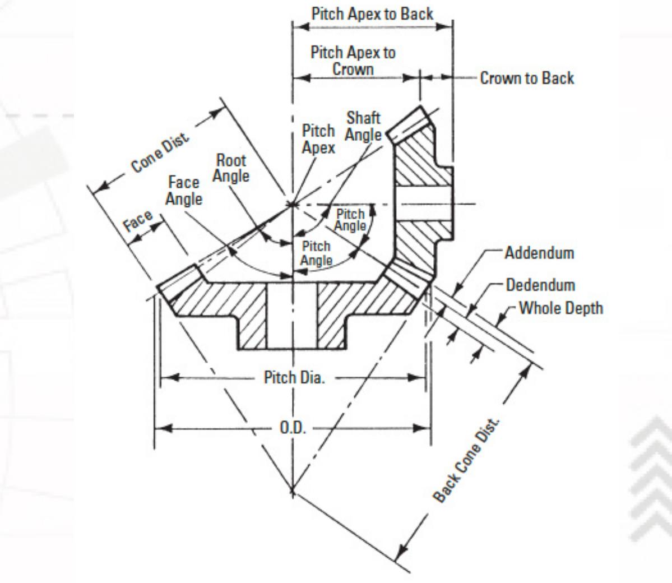
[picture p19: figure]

Figure 21: Reference diagram for gear calculations

Sℎaft Angle(θ) = 90 degrees

Gear ratio = 4: 1

Number of Teetℎ − pinion (zp) = 16

Number of Teetℎ − base (zb) = 64

Pitcℎ diameter − pinion (dp) = 27.94 mm

Pitcℎ diameter − base (db) = 111.76 mm

Module (m) =

db
zb

= 1.746

Pitcℎ angle − pinion (αp) = tan⁻¹

( sinθ/ ((

zp
zb

) + cosθ)) = 14.04 degrees

Pitcℎ angle − base (αb

) = θ − αp = 75.96 degrees

Face (b) = 6.86 mm

Addendum − base (ℎb

) = 0.540m +

0.460m
(

zbcosαp
zpcosαb

)

= 2 mm

Addendum − pinion (ℎp) = 2.00m − ℎb = 1.5 mm

Dedendum − pinion (fp) = 2.188m − ℎp = 2.32 mm

Dedendum − base(fb

) = 2.188m − ℎb = 1.82 mm

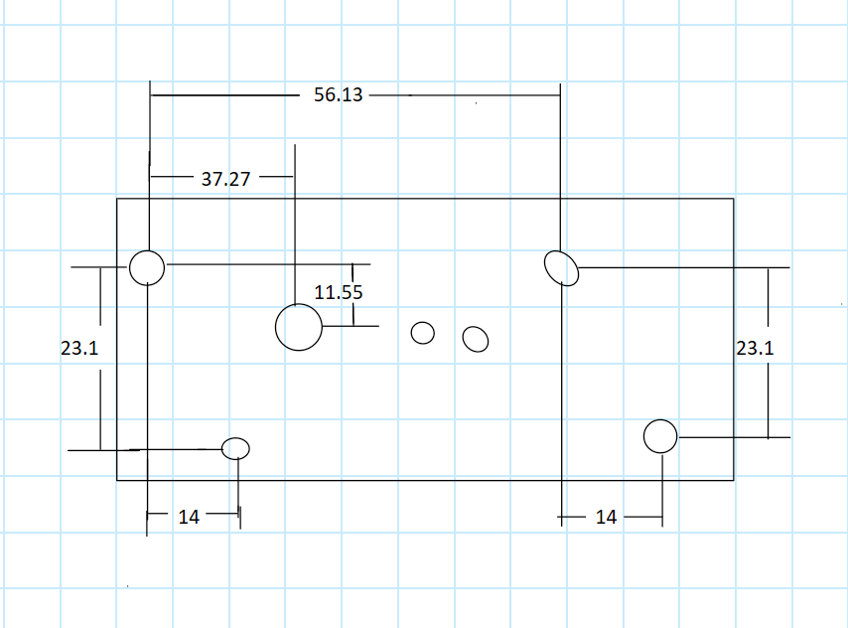
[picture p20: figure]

Figure 22: Measurements for hole placements on the motor mount and mounting plate. All measurements in millimeters.

## Appendix V: Evaluation Rubric

Table 6: Evaluation Rubric for the Testing Phase for the Model.

Score: | Motion Study | Static Analysis | Sustainability | Financial Requirements
1 | m -Required velocity of 1 s or less. | -Can sustain a load of 1kg -Area is more than 25”x25” | Carbon footprint of more than 6kg after four years of use. | -Total cost exceeds $100. -5 or fewer printing sessions were done.
2 | m -Required velocity of 2 s or more. | -Can sustain a load of 2kg -Area is more than 20”x20” | Carbon footprint of around 4kg or less after 4 years of use. | -Total cost is $85 or less. -4 or fewer printing sessions were done.
3 | m -Required velocity of 3 s or more. | -Can sustain a load of 3kg -Area 18”x18” or less | Carbon footprint of around 3kg or less after four years of use. | -Total cost is about $71 (predicted amount). -3 or fewer printing sessions were done.
4 | -Required acceleration of less than 12m s 2 m -Required velocity of 4 s or more. | -Can sustain a load of 4kg -Area is 16”x16” or less | Carbon footprint of around 2kg or less after 4 years of use. | -Total cost is $70 or less. -Two or fewer printing sessions were done.
5 | -Required velocity of m more than 5 . s | -Can sustain a load of 5kg -Area is 15”x15” or less | Carbon footprint of around 1kg or less after 4 years of use. | -Total cost is $60 or less. -Only one printing session was needed.

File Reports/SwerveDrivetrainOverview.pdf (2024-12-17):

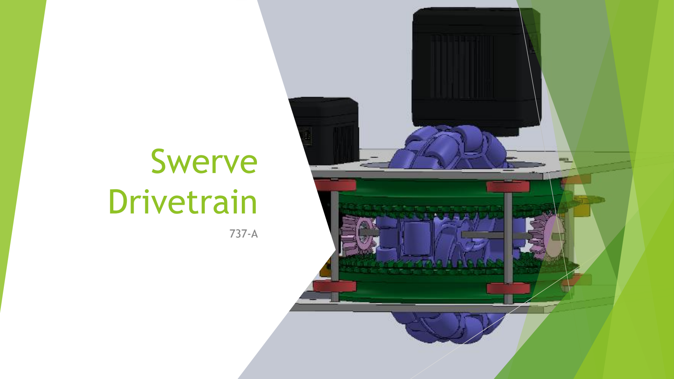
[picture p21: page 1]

# Swerve Drivetrain

737-A

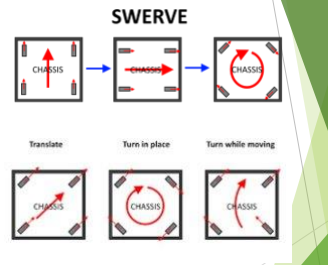
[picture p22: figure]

# What is a Swerve Drivetrain?

## - Able to strafe in all directions

## - Able to rotate wheels in the direction of movement

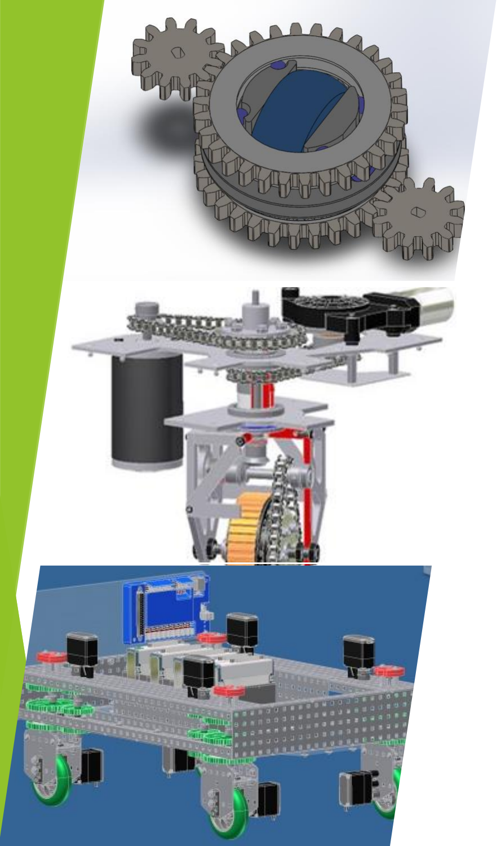
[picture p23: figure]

# Design Ideas

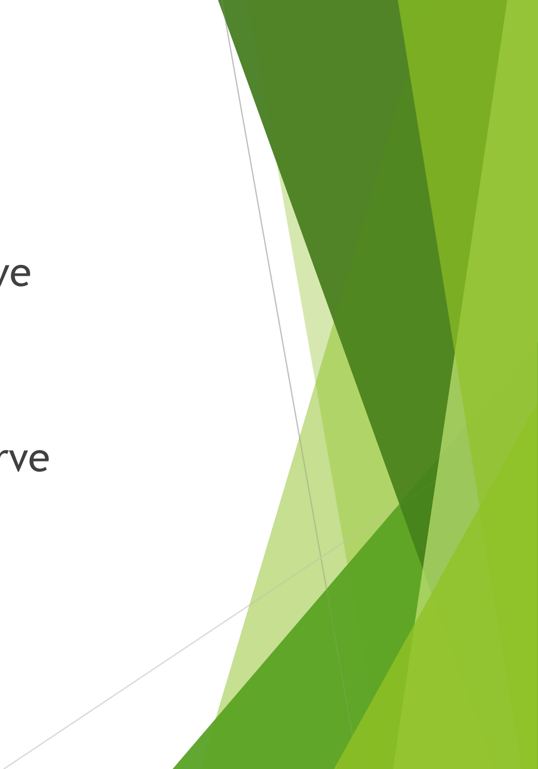
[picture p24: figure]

## - Differential Swerve

## - Transmission Swerve

## - Direct Drive

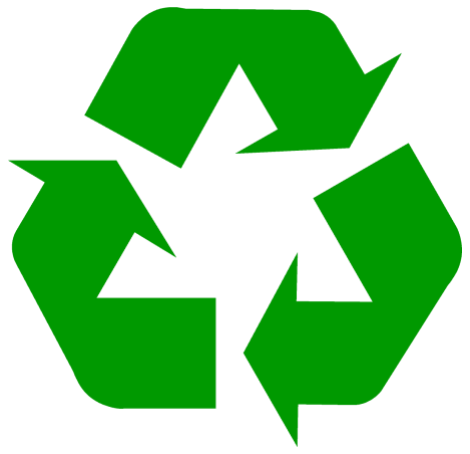
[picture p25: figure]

# Considerations When Choosing a Design


-Financial cost per design

-Reusing parts from old robots

-Attachment for use in further projects

Completing the Design; Many smaller decisions needed to be made; •Gear supports •Power transmission; Needed a plan to acquire VEX-legal parts; •Only able to use radial bearings

Preliminary Design Calculations; gears; Calculations are all connected; Everything starts by picking an inner diameter and a gear ratio; pinion gear size, and tooth depth is calculated using set equations

- Key system of the design were the custom-built
- They are the base that everything builds off
- Everything else, including teeth angles,

# Key Design Parameters


- Needed to fit the 4-inch wheels inside the gears
- Targeting a 4:1 gear ratio from our research


# Designing

- Gears were then designed in SolidWorks and modelled using an assembly to ensure proper alignment
- Mounting plates and motor mounts were also assembled separately using the spacing determined by the
calculations


# Challenges

## - Incompatible parts

- CAD files required to be completed before the parts list was created

## - 4" omnidirectional wheel does not have a 4" diameter

## - QVEX team could only provide Vex high-strength chains


## Swapped omnidirectional wheel for a standard Vex wheel


# Solutions

## Chains were replaced with gears

## CAD file for compatible gears was found and 3D printed

## Mounting plate was altered to accommodate for the loss of chains


# Building

## - Began by machining the mounting plates with the altered hole placements

## - Sharp edges were sanded and covered in electrical tape

## - Mounting plates are thin and warped under the force of machining

## - The gear teeth interfere with the bearing shafts

Testing; • Testing was done through various simulations in SolidWorks • Diagrams represent the load distribution of a 270N weight (weight of a robot)

# Testing: Motion Study


Driving

Rotating

Using the gear ratio of
18:64, the model
achieved a constant
velocity of 3.59 m
s

# Analysis of Results

## Goals

1. Velocity of 5 m/s
2. Improved strength
3. Decrease in size

## Recommendations

1. Use chains to allow flexibility within gear ratios
2. Properly machine mounting plates from thicker metal to provide a stronger base


3. Position motors closer together

Implementation; Using a larger metal sheet, template will be cut four times in each corner; Metal pieces will be welded together; Smaller bearing axles; main chassis

- Bolts used to attach mounting plate to


# Questions?

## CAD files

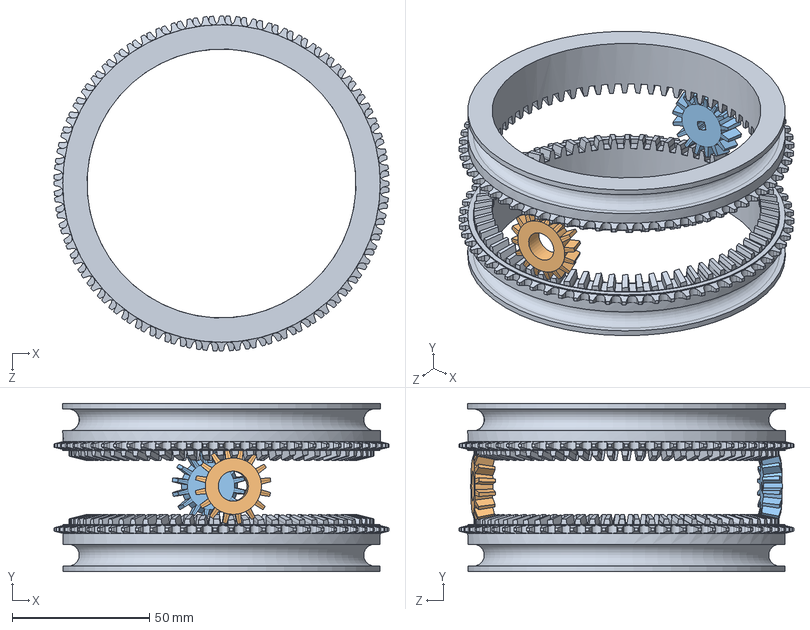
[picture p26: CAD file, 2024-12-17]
Solidworks Files/Drivetrain/GearCore.SLDASM
122.1 x 61.3 x 122.1 mm
BASE_GEAR x 2
PinionNeedingBearing
PinionGear

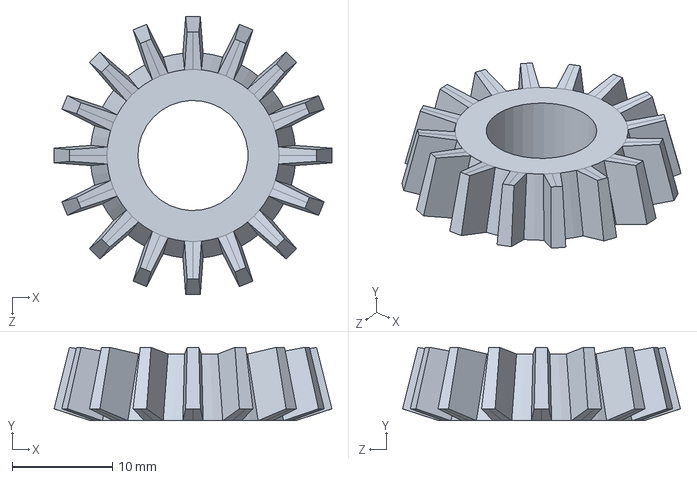
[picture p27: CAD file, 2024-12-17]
Solidworks Files/Motion Study/BearingPinion.SLDASM
27.8 x 7.33 x 27.8 mm

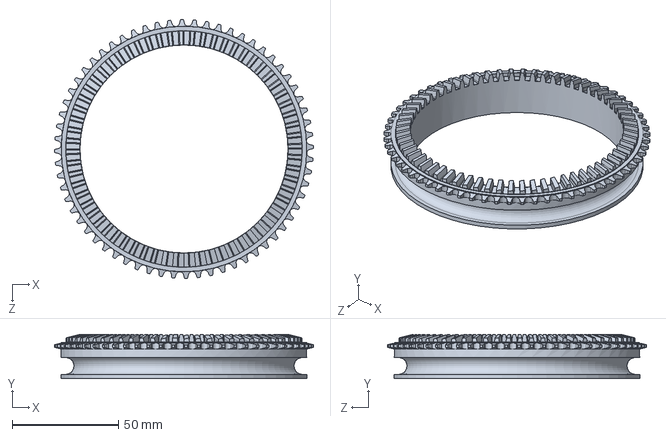
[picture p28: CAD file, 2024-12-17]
Solidworks Files/Motion Study/BASE_GEAR.SLDPRT
122.1 x 20.9 x 122.1 mm

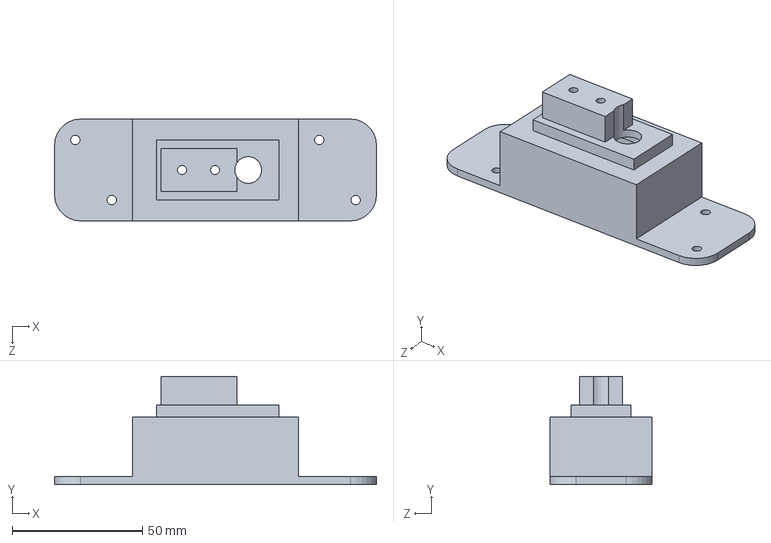
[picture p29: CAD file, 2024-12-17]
Solidworks Files/Drivetrain/Motor mount final.SLDPRT
123.6 x 41.5 x 39.1 mm

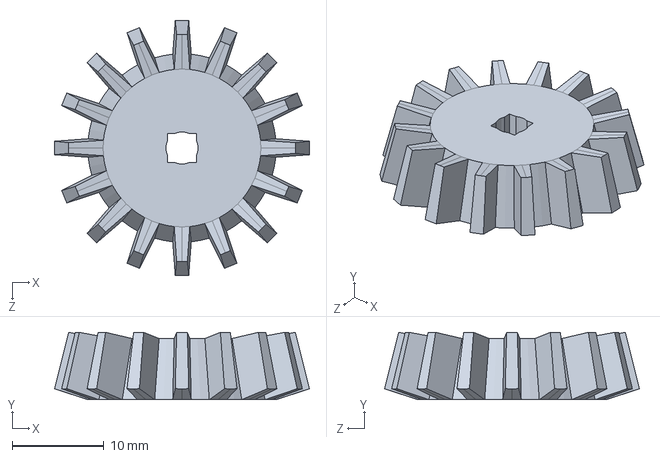
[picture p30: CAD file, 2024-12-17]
Solidworks Files/Drivetrain/PinionGear.SLDPRT
27.8 x 7.33 x 27.8 mm

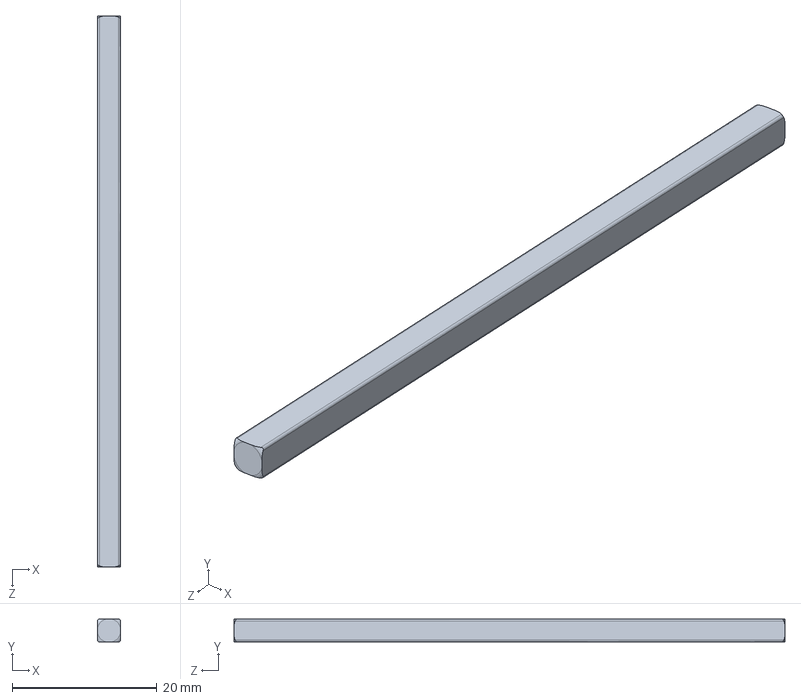
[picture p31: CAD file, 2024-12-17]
Solidworks Files/Motion Study/3 Shaft (276-2011-002).step.SLDPRT
3.17 x 3.17 x 76.2 mm

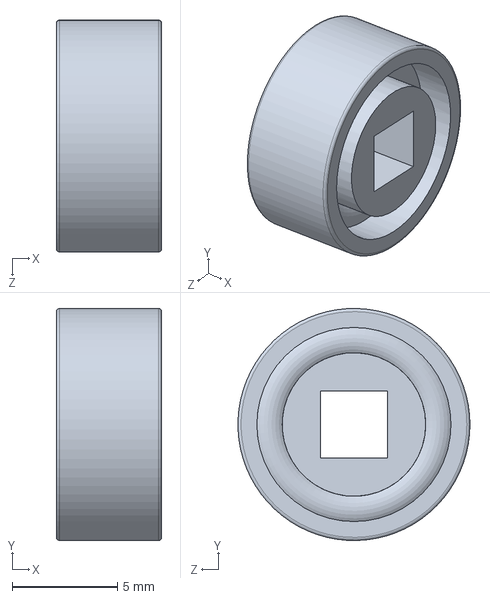
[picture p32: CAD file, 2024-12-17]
Solidworks Files/Drivetrain/REAL_BEARINGGGGG.SLDPRT
5.00 x 11.0 x 11.0 mm

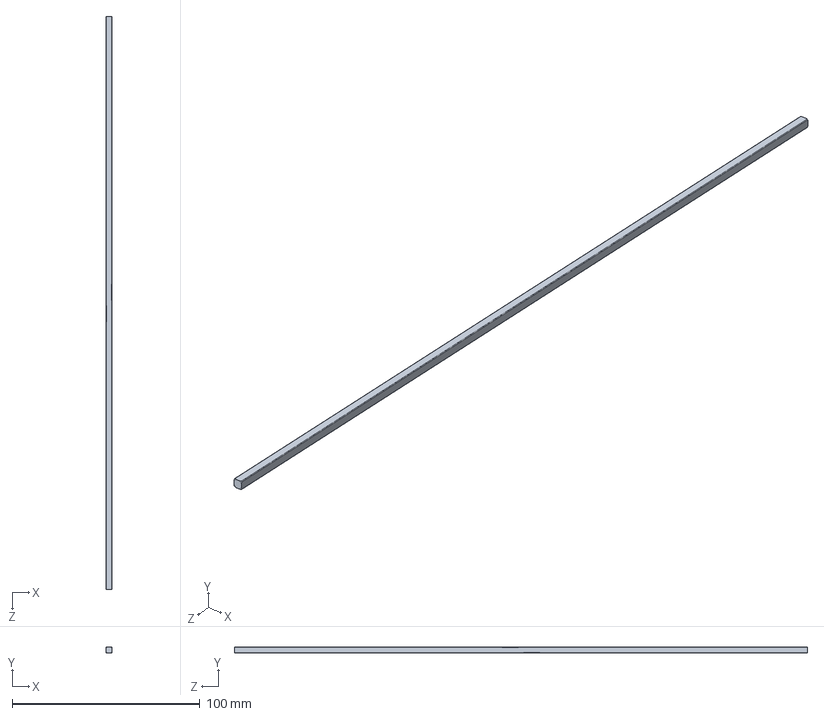
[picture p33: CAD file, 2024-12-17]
Solidworks Files/Drivetrain/Drive Shaft 12 (276-1149).step.SLDPRT
3.17 x 3.17 x 304.8 mm

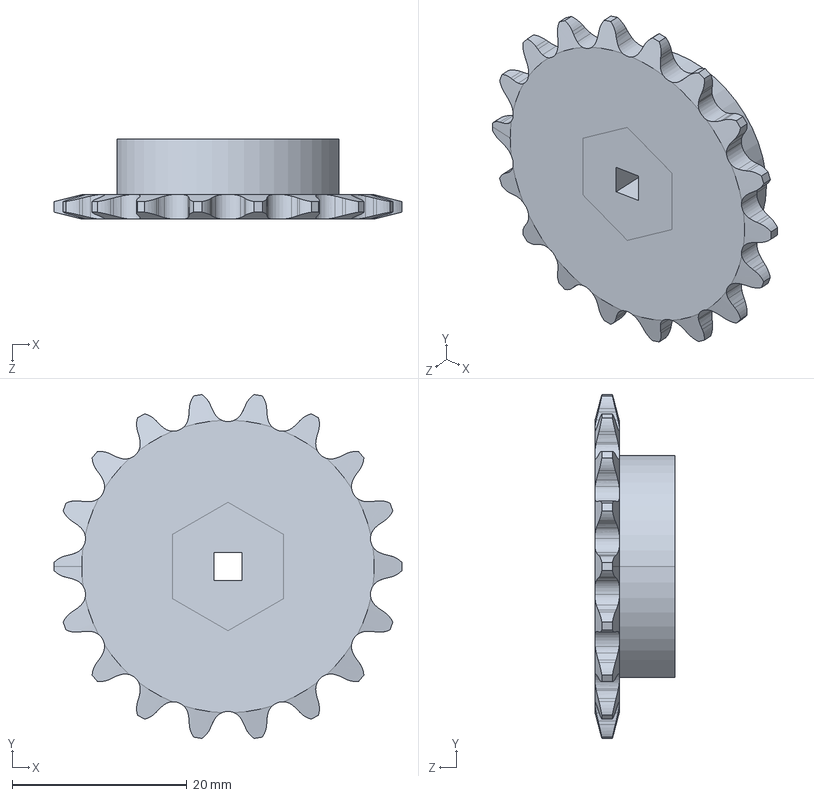
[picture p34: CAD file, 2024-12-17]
Solidworks Files/Drivetrain/18T Sprocket.SLDPRT
39.8 x 39.4 x 9.18 mm

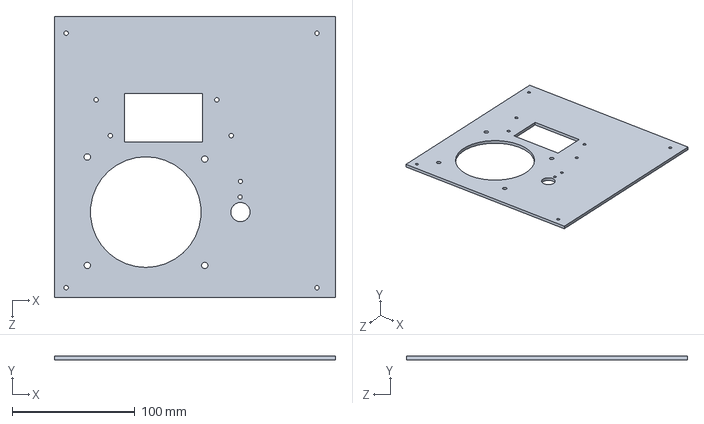
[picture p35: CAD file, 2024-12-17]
Solidworks Files/Drivetrain/mounting plateee.SLDPRT
228.6 x 3.43 x 228.6 mm

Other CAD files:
Solidworks Files/Drivetrain/BearingPinion.SLDASM
Solidworks Files/Motion Study/PinionGear.SLDPRT
Solidworks Files/Drivetrain/BASE_GEAR.SLDPRT
Solidworks Files/Motion Study/PinionNeedingBearing.SLDPRT
Solidworks Files/Drivetrain/PinionNeedingBearing.SLDPRT
Solidworks Files/Drivetrain/Drive Shaft 12 (276-1149).step
